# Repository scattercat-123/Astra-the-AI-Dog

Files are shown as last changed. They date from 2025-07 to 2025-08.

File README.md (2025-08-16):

# Astra-the-AI-Dog 🐶
Me making a quadruped robot dog companion.
Check the Journal.md file for more info.

## Bom:
|No.|Parts |Quantity  |Price in rupees|Price in Dollars|Buying link |Notes |
|---|---|---|---|---|---|---|
|1  |XT30 + 2 |12 |₹588.00 |$6.81 |https://robu.in/product/amass-xt3022-female-connector-xt3022-f-g-b/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|This is for connecting power and canbus to motor|
|2  |Carbon Fiber tube for leg|2 x 1meter|₹3,398.00 |$39.33 |https://uavgarage.com/product/3k-roll-wrapped-carbon-fiber-tube-hollow20mmod18mmid500mml/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 | |
|3  |Motors (bruh) |12 |₹43,000.00 |$500.56 |alibaba | |
|4  |Orange PETG |1kg |₹1,200.00 |$13.89 |https://robu.in/product/esun-epetghs-filament-1-75mm-solid-orange-1kg-roll-with-paper-roll/ |For the orange parts |
|5  |Black PETG |1kg |₹1,200.00 |$13.89 |https://robu.in/product/esun-epetghs-3d-printing-filament-1-75mm-solid-black/ |For black parts |
|6  |Silicone 30A for feet |1 |1299 |$15.03 |https://www.amazon.in/RANA-POLYMERS-Silicone-RTV-Platinum/dp/B0F8HLM46L?th=1 | |
|7  |Rpi 5 |1 |I already have |- |- | |
|8  | | | | | | |
|9  |TOTAL | |₹50,685.00 |$580.50 | | |

## How does this work:

Here the side motor drives the whoe thing whih is connected on the bearing.

This motor, drives the hip joint of the leg.
For the knee motor, i have researched on many papers which claim when the motors is placed far from the hip join the torque provided by the hip joint is needed more so the battery gets drained fast. You can see the knee system here:


THats all and i just did lot of harware electroncis components selections too.

This is an ai dog which is designed for hackclub highway.
Here are some sneek peaks:





⭐ The repo if you like it!
I am going to upload future updates about the dog, including a whole youtube playlist after buying the parts. Make sure to stay tuned in!

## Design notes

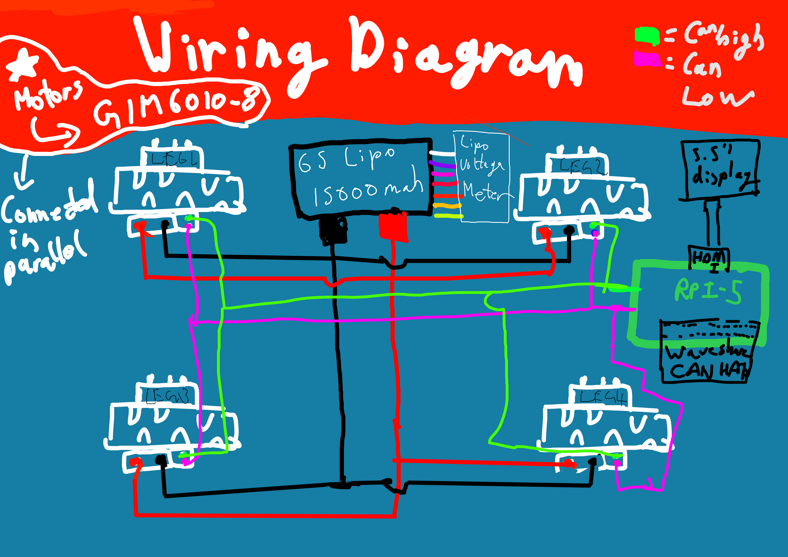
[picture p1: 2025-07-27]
Schematic Of Astra.png

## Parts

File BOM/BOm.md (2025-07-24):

# YOu can view the bom [here](https://docs.google.com/spreadsheets/d/1tXSbPTXzO7x9RjKfoS4aTnTzwVyE0GcGUCTSj2ZbIsA/edit?usp=sharing) or check the .csv in this folder..

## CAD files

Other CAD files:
CAD/Leg Design v19.step
CAD/Astra The AI Robotic Dog v4.step

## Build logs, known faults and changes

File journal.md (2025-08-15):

# Astra: The AI Quadruped dog

**Total time spent:** ~46 hours over 13 days  
<hr>

## What is this?
 - A dog which acts as a companion robot dog.
 - Uses Actuators with planetary gearbox and multiple sensor for advanced AI!
 - Using jetson nano orin super (raspberry pi using for testing)!!!
<hr>

## Day 1: Research and starting fusion — *5 hrs*
I have already researched enough­. imma start.  
Opened fusion, set up a new project and started with the leg design.  
Okay im using carbon fiber rods for the leg! I chose carbon fiber because it’s super strong and lightweight so the motors don’t need to work as hard.  

And for the foot im using a silicon molded ball thing :suspect:  
  

A somewhat completed foot 🦶. I made the socket in fusion so the ball can snap in tightly but still move a bit to absorb shocks. Modeled a curved base so the silicone grips the floor better. This will help the dog run without slipping.  

## Day 2: I dint show you something b4 — *6 hrs*
I actually had started designing 2 ACTUATORS. One was using a [camera motor](https://shop.iflight.com/ipower-motor-gm5208-12-brushless-gimbal-motor-pro279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) - i forgot whats that called. but that only had 2.5kg/cm which i had observed after an entire day.  
I modeled the casing, made a basic planetary gearbox to try boosting torque, and even planned the mount holes.  

Faliure photo :( -  
  

I was going to make like a planetary gearbox but nvm.. torque too low so pointless.  

Then i thought i would use the eaglepower 90kv motor just like [Aaed Musa](https://www.aaedmusa.com/). I designed a custom gearbox for it in fusion, added space for a magnetic encoder, and was almost done. But later i realised it would become too expensive after me buying odrive s1's.  

So i went on alibaba and the chepaest thing which i found which has an encoder and driver built into it was this motor  

THE GIM6010-8!!!!!!!!!!!!!!!!!!!!!!  
This was the perfect motor because it had a stall torque of 11n.m and the motor was tested by someone over [here](https://hackaday.io/project/202366-the-unnamed-spider-bot/log/239789-steadywin-gim6010-8-stock-controller-vs-odrive-vs-tinymovr)  
Also this has a driver and it has like planetary gaerbox in it. so this was perfect. and it was kinda cheap. bruh - 70$ 💸  
Can someone help me rob a bank 💰.. jkjk dont call 911  
Yeah, wasted i gues 3-4 days on deciding a motor.

## Day 3-5: Designed something :) — *12 hrs total*
  

If you can see these are gt2 belts. so like the motor will stay on the hip but drive the knee axis.  
I modeled the motor bracket, belt pulleys, and tensioner in fusion so the belt stays tight even after long use.  
This is actually useful because research showed that the battery would drain faster if the motor was near the knee because of incraesed weight 🤓. So yeah, moving the motor higher saves energy and reduces leg inertia.  

## Day 5-10: did very little stuff — *8 hrs total*
Im very distracted. but I still made the knee, hip, and abduction joint (aka moves your lige side to side) models ready in fusion.  

Here’s some final thingies for all axis -  
  
  
  
  

So basically the leg was done! I modeled every mounting hole, designed bearing housings for smooth motion, and made space for the belts to run without rubbing.  
Also added attachment points for the carbon fiber rods so they can slide in and be locked with screws.

## Day 10: Dont ask me why is this so complex.. — *3 hrs*
Yeah i just realized it would be hard to 3d print and assemble some parts. so fixed my issues!  
Went back in fusion, split some parts into two pieces so they can fit on my printer bed, added alignment pins so they fit perfectly when assembled. Also thickened a few parts for strength and added more space for tools to reach bolts.

## Day 11-13: Final Full dog design. — *10 hrs total*
Today I designed my almost complete dog.  
  

I took the individual legs and assembled them onto a main body frame in fusion.  
Designed the body plates with holes for ventilation and mounts for electronics. Made space in the center for battery and Jetson Nano Orin Super (and Pi for now).  
Also made sapace for all cables and all uk
Even added small brass inserts for frame strength because carbon rods + 3D parts can flex if not supported.  

I also finished my overly expensive [BOM](https://docs.google.com/spreadsheets/d/1tXSbPTXzO7x9RjKfoS4aTnTzwVyE0GcGUCTSj2ZbIsA/edit?gid=0#gid=0).  
Right now i am not adding sensor mounts and all to my dog since i will test my ai stuff and then add sensors and all for autmoated dog exploration.

I am not sure if it looks good. But remember to star my repo ⭐

## Day 11: Final stuff — *2 hrs*
Some final adjustments, submitted in highway pitstop channel.  
Double checked the belt alignment in fusion using the joint animation feature to see if there’s any clash. Printed some test pulleys to see if they fit the belt perfectly.  
Tweaked bolt hole sizes for M3 hardware so I don’t have to force them in later.  
Feeling good about this now.

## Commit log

2025-07-23 cad.md v1.0
2025-07-23 Added cad
    [Astra The AI Robotic Dog v4.step, Leg Design v19.step]
2025-07-23 add cad
    [Leg Design v19.step]
2025-07-24 Aded the very overpriced bom to my repo
    [Astra The Robot Dog _ BOM - Sheet1.csv]
2025-07-27 Schematic if you need reference! bruh ik its not neat
2025-07-27 added bom outside the bom folder cause some ppl cant find it
    [Astra The Robot Dog _ BOM - Sheet1.csv]
2025-08-07 added bom
2025-08-15 added bom to readme
2025-08-15 expanded bom
2025-08-16 Update Astra The Robot Dog _ BOM - Sheet1.csv
    [Astra The Robot Dog _ BOM - Sheet1.csv]
